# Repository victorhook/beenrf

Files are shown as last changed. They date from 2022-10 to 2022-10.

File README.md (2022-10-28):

# BeeNrf BeeNrf logo

## How to get started with EFM8B Busy Bee Ubuntu 22.04

### 1. Install stable wine.
Install wine according to winehq: https://wiki.winehq.org/Ubuntu
Don't follow normal ubuntu guidelines, since it requires manually installing `wine32`
which wants to break half of my system.

### 2. Launch
cd $SIMPLICITY_INSTALLATION && WINEPATH=$SIMPLICITY_INSTALLATION ./studio

## BOM
| Geared 3V motor x2 | 32kr * 2 |
| Front wheel |  |
| nrf24l01 | 18kr | 
| Busy Bee 8-bit | 10kr |
| Mosfet | 2 |
| Battery charg | |

## PCB Layers
1. RF signals
2. Ground  <- Don't break!
3. Power   <- Don't break!
4. Other signals

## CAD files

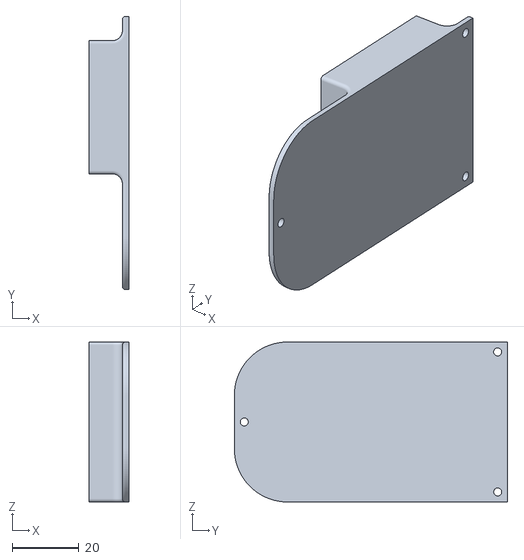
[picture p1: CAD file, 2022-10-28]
cad/Robot-Top.stl
12.0 x 82.0 x 48.0

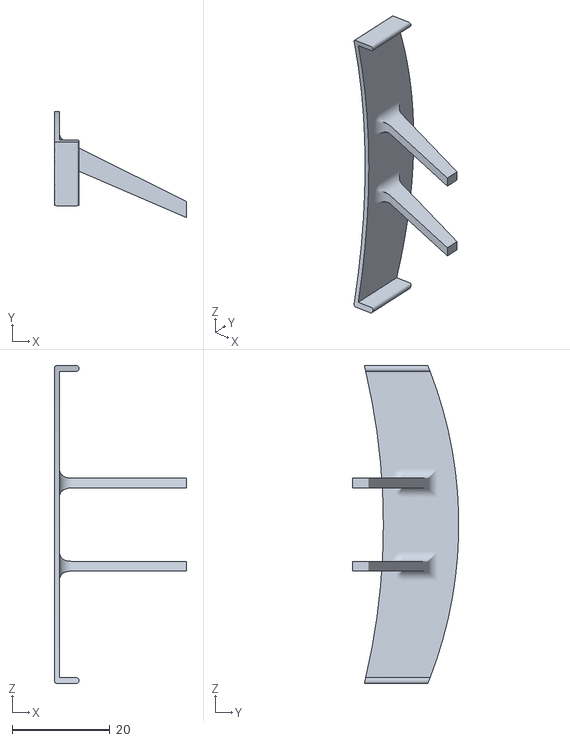
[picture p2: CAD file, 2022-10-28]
cad/Robot-Spoiler.stl
27.0 x 21.7 x 65.0

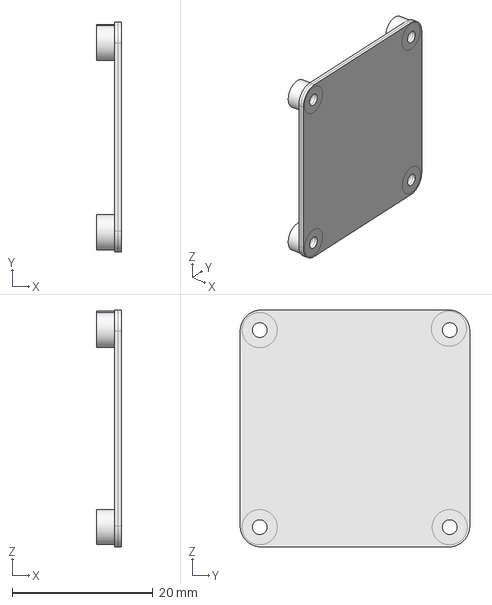
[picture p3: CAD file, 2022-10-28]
cad/Robot.FCStd
3.50 x 32.6 x 33.7 mm

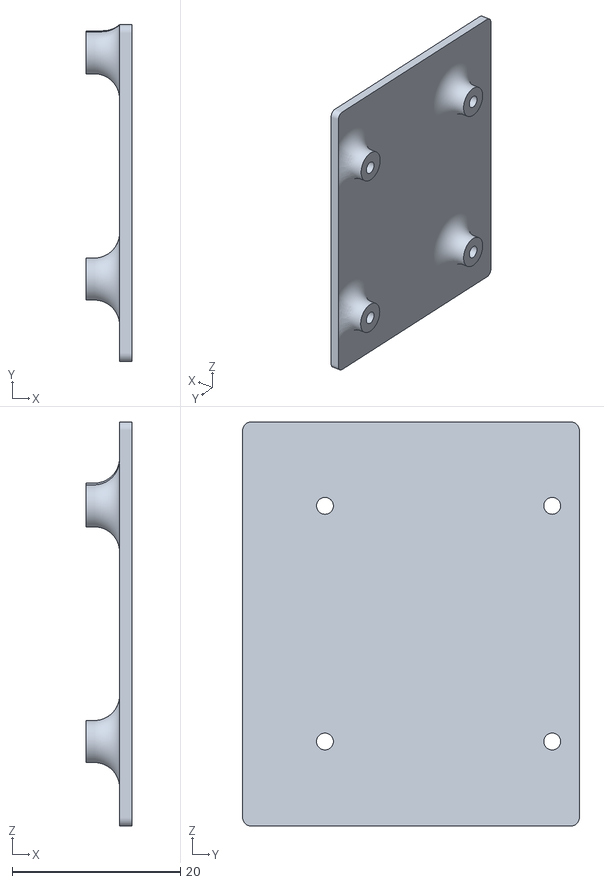
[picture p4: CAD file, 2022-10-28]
cad/Robot-TopsTop.stl
5.50 x 40.0 x 48.0

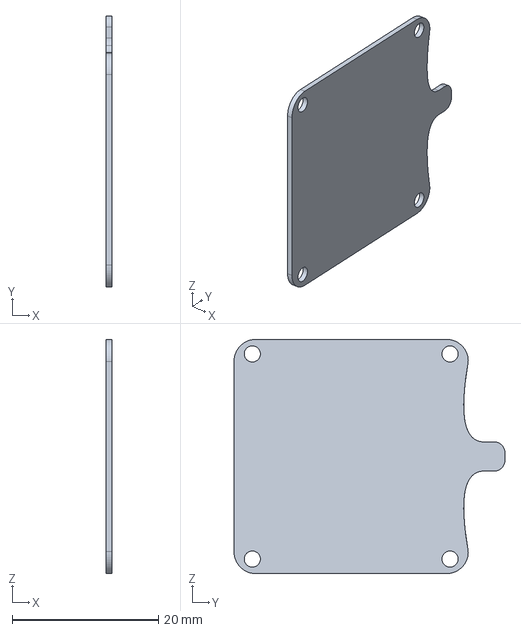
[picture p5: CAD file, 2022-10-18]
cad/Fillet004.step
0.8 x 37.0 x 32.0 mm

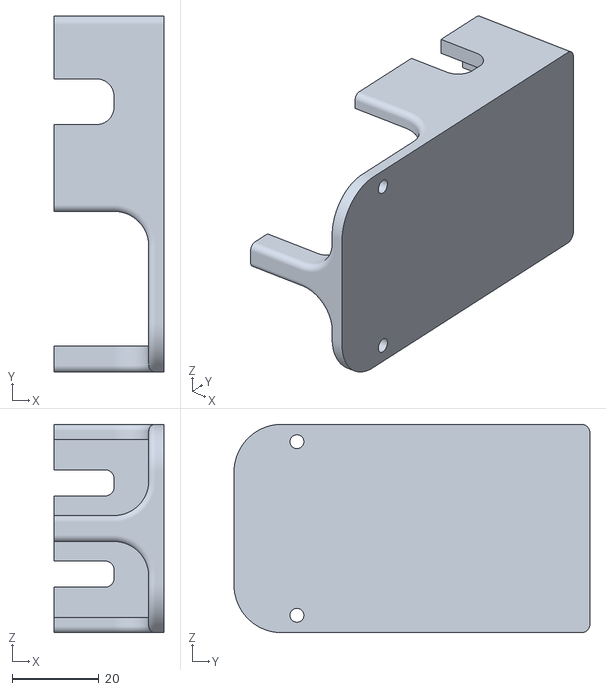
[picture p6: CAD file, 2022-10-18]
cad/Robot-Bottom.stl
25.3 x 82.0 x 48.0

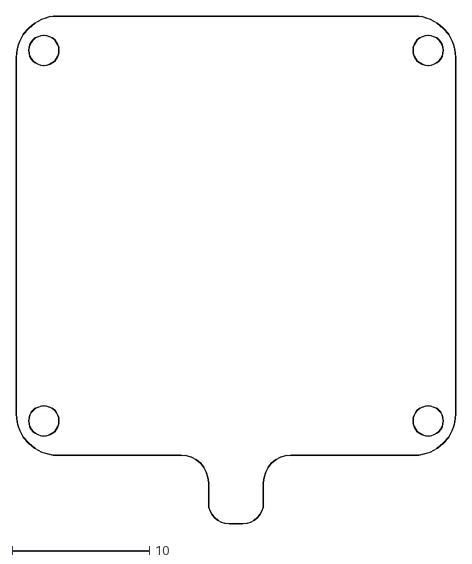
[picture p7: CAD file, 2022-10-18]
cad/PCB.dxf
32.0 x 37.0

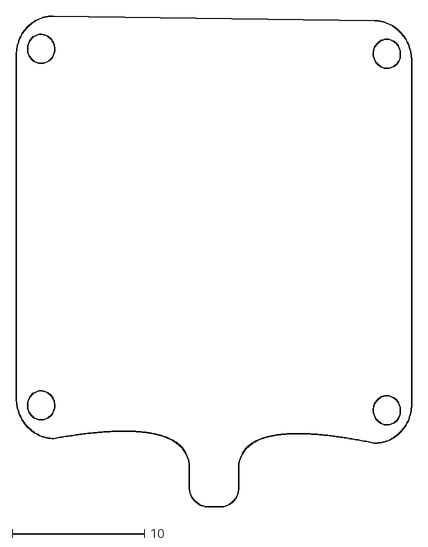
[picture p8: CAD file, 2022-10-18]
cad/Robot-Shape2DView002.dxf
29.9 x 37.2

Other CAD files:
cad/Robot-TopTopTop.stl

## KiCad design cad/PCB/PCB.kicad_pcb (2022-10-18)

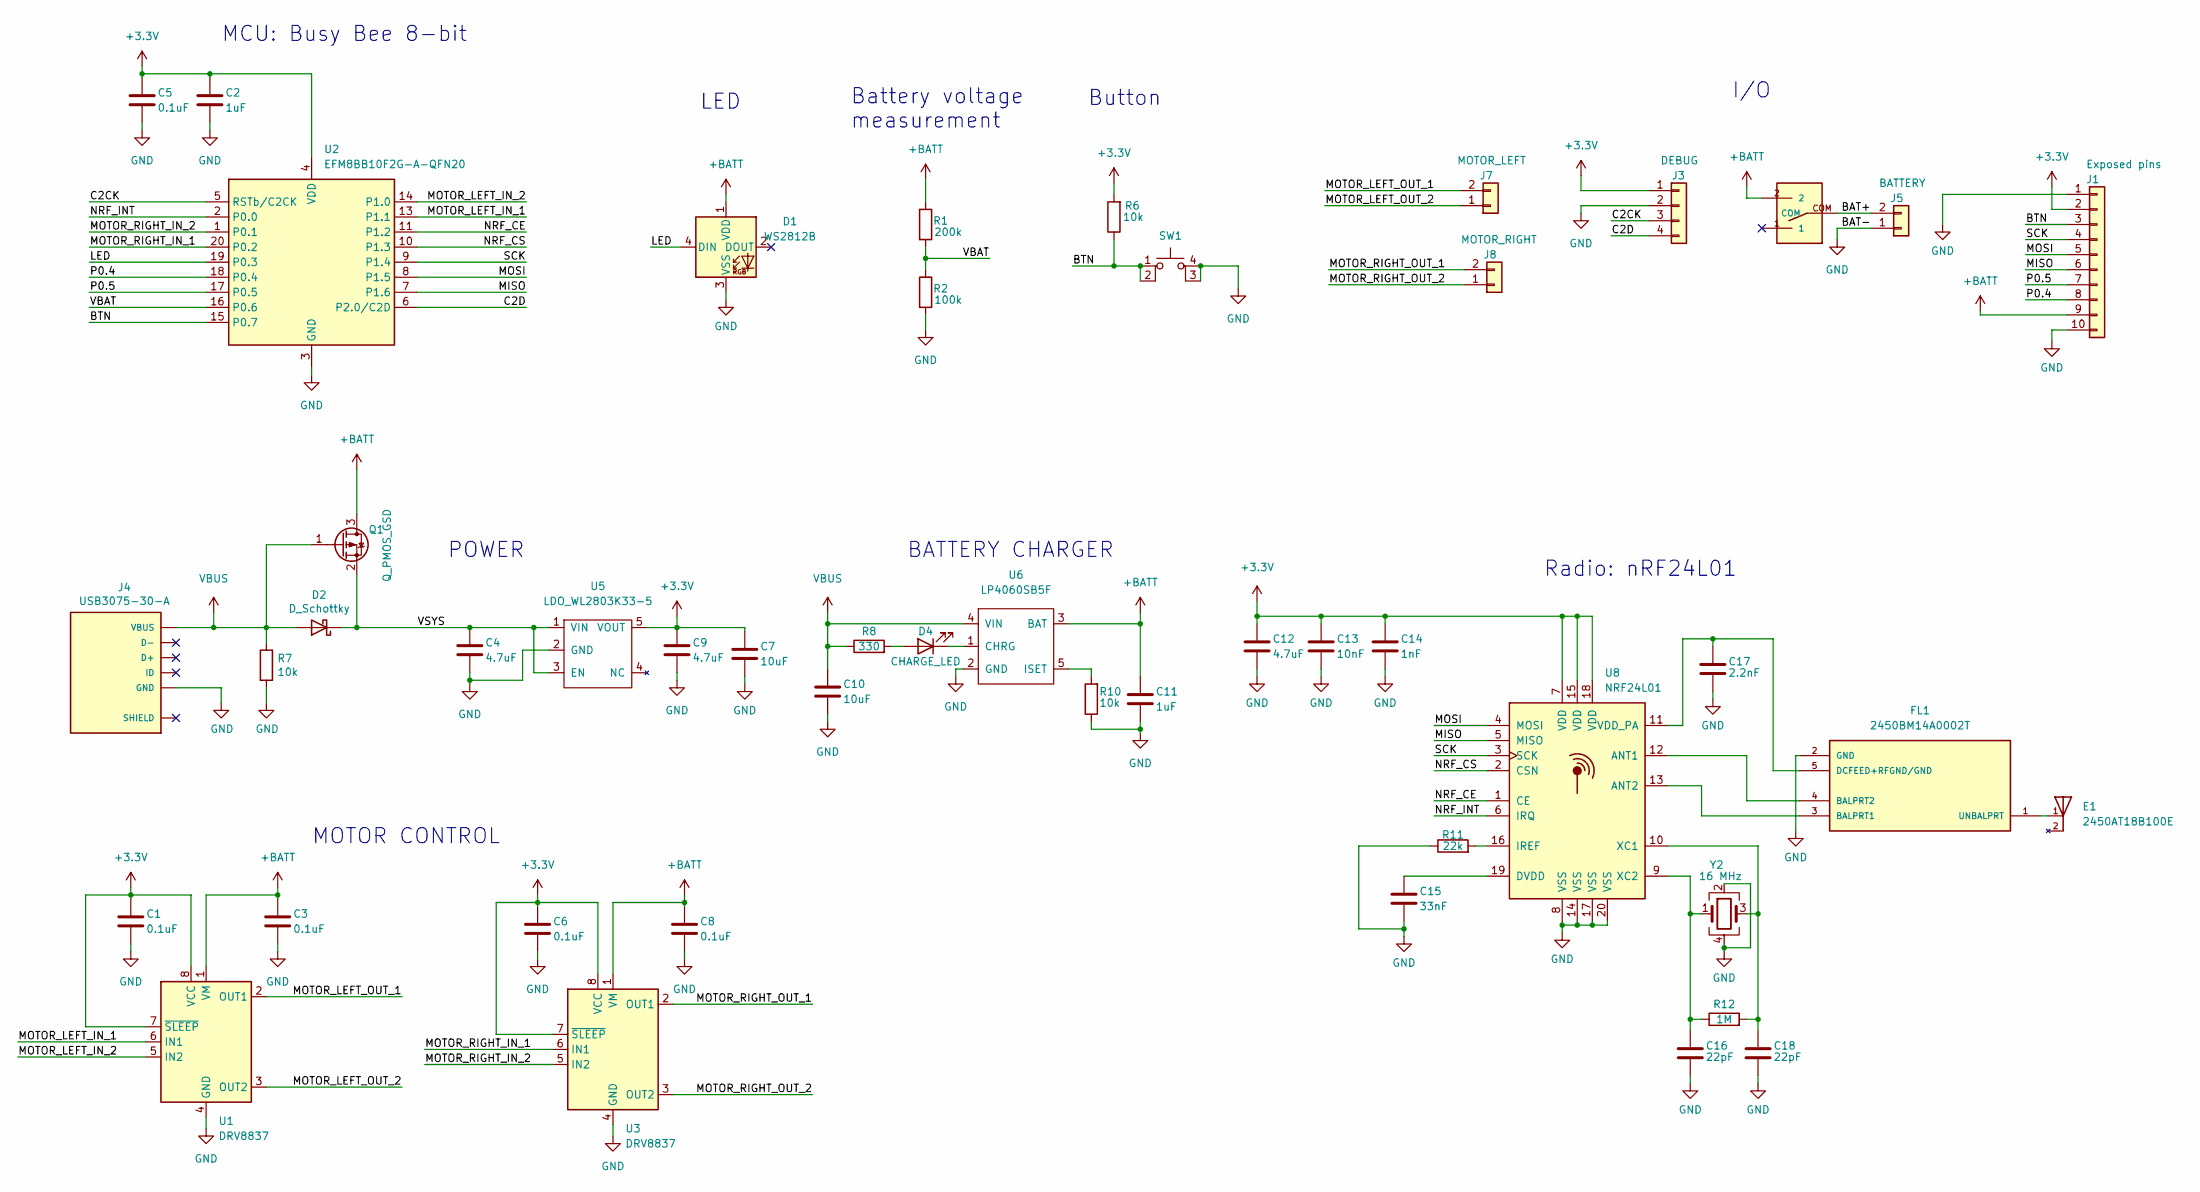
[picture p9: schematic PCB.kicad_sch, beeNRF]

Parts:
C1, C3, C5, C6, C8: 0.1uF; C_0402_1005Metric
C2, C11: 1uF; C_0402_1005Metric
C4, C9, C12: 4.7uF; C_0402_1005Metric
C7, C10: 10uF; C_0805_2012Metric
C13: 10nF; C_0402_1005Metric
C14: 1nF; C_0402_1005Metric
C15: 33nF; C_0402_1005Metric
C16, C18: 22pF; C_0402_1005Metric
C17: 2.2nF; C_0402_1005Metric
D1: WS2812B; LED_WS2812B_PLCC4_5.0x5.0mm_P3.2mm
D2: D_Schottky; D_SOD-123
D4: CHARGE_LED; LED_0603_1608Metric
E1: 2450AT18B100E; 2450AT18B100E_pcb_antenna; PARTREV 4.0
FL1: 2450BM14A0002T; 2450BM14A0002; PARTREV 6/13/2012
J1: Exposed pins; PinSocket_1x10_P2.54mm_Vertical
J3: DEBUG; JST_SH_SM04B-SRSS-TB_1x04-1MP_P1.00mm_Horizontal_No_silk
J4: USB3075-30-A; PARTREV D3
J5: BATTERY; Conn_01x02_VBAT
J7: MOTOR_LEFT; Conn_01x02_VBAT
J8: MOTOR_RIGHT; Conn_01x02_VBAT
Q1: Q_PMOS_GSD; SOT-23
R1: 200k; R_0402_1005Metric
R2: 100k; R_0402_1005Metric
R6, R7, R10: 10k; R_0402_1005Metric
R8: 330; R_0402_1005Metric
R11: 22k; R_0402_1005Metric
R12: 1M; R_0402_1005Metric
SW1: RESET; PTS815
U1, U3: DRV8837; WSON-8-1EP_2x2mm_P0.5mm_EP0.9x1.6mm
U2: EFM8BB10F2G-A-QFN20; SiliconLabs_QFN-20-1EP_3x3mm_P0.5mm_EP1.8x1.8mm
U5: LDO_WL2803K33-5; SOT-89-5
U6: LP4060SB5F; SOT-23-5
U7: SK12D07VG4; toggle_switch_SK12D07VG4
U8: NRF24L01; QFN-20-1EP_4x4mm_P0.5mm_EP2.5x2.5mm
Y2: 16 MHz; Crystal_SMD_2520-4Pin_2.5x2.0mm

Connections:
+3.3V: C1.1, C2.1, C5.1, C6.1, C7.1, C9.1, C12.1, C13.1, C14.1, J1.2, J3.1, R6.2, U1.7 (~SLEEP), U1.8 (VCC), U2.4 (VDD), U3.7 (~SLEEP), U3.8 (VCC), U5.5 (VOUT), U8.7 (VDD), U8.15 (VDD), U8.18 (VDD)
+BATT: C3.1, C8.1, C11.1, D1.1 (VDD), J1.9, Q1.3 (D), R1.1, U1.1 (VM), U3.1 (VM), U6.3 (BAT), U7.2
/BAT+: J5.2, U7.COM
/BTN: J1.3, R6.1, SW1.1, SW1.2, U2.15 (P0.7)
/C2CK: J3.3, U2.5 (RSTb/C2CK)
/C2D: J3.4, U2.6 (P2.0/C2D)
/LED: D1.4 (DIN), U2.19 (P0.3)
/MISO: J1.6, U2.7 (P1.6), U8.5 (MISO)
/MOSI: J1.5, U2.8 (P1.5), U8.4 (MOSI)
/MOTOR_LEFT_IN_1: U1.6 (IN1), U2.13 (P1.1)
/MOTOR_LEFT_IN_2: U1.5 (IN2), U2.14 (P1.0)
/MOTOR_LEFT_OUT_1: J7.2, U1.2 (OUT1)
/MOTOR_LEFT_OUT_2: J7.1, U1.3 (OUT2)
/MOTOR_RIGHT_IN_1: U2.20 (P0.2), U3.6 (IN1)
/MOTOR_RIGHT_IN_2: U2.1 (P0.1), U3.5 (IN2)
/MOTOR_RIGHT_OUT_1: J8.2, U3.2 (OUT1)
/MOTOR_RIGHT_OUT_2: J8.1, U3.3 (OUT2)
/NRF_CE: U2.11 (P1.2), U8.1 (CE)
/NRF_CS: U2.10 (P1.3), U8.2 (CSN)
/NRF_INT: U2.2 (P0.0), U8.6 (IRQ)
/P0.4: J1.8, U2.18 (P0.4)
/P0.5: J1.7, U2.17 (P0.5)
/SCK: J1.4, U2.9 (P1.4), U8.3 (SCK)
/VBAT: R1.2, R2.1, U2.16 (P0.6)
/VSYS: C4.1, D2.1 (K), Q1.2 (S), U5.1 (VIN), U5.3 (EN)
GND: C1.2, C2.2, C3.2, C4.2, C5.2, C6.2, C7.2, C8.2, C9.2, C10.2, C11.2, C12.2, C13.2, C14.2, C15.2, C16.2, C17.2, C18.2, D1.3 (VSS), FL1.2 (GND), J1.1, J1.10, J3.2, J4.5 (GND), J5.1, R2.2, R7.2, R10.1, R11.1, SW1.3 (K), SW1.4 (A), U1.4 (GND), U1.9 (GND), U2.3 (GND), U2.12 (GND), U2.21 (GND), U3.4 (GND), U3.9 (GND), U5.2 (GND), U6.2 (GND), U8.8 (VSS), U8.14 (VSS), U8.17 (VSS), U8.20 (VSS), Y2.2, Y2.4
unnamed: C15.1, U8.19 (DVDD)
unnamed: C16.1, R12.1, U8.9 (XC2), Y2.1
unnamed: C17.1, FL1.5 (DCFEED+RFGND/GND), U8.11 (VDD_PA)
unnamed: C18.1, R12.2, U8.10 (XC1), Y2.3
unnamed: D4.1 (K), U6.1 (CHRG)
unnamed: D4.2 (A), R8.2
unnamed: E1.1, FL1.1 (UNBALPRT)
unnamed: FL1.3 (BALPRT1), U8.13 (ANT2)
unnamed: FL1.4 (BALPRT2), U8.12 (ANT1)
unnamed: R10.2, U6.5 (ISET)
unnamed: R11.2, U8.16 (IREF)
VBUS: C10.1, D2.2 (A), J4.1 (VBUS), Q1.1 (G), R7.1, R8.1, U6.4 (VIN)

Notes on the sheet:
Battery voltage measurement
BATTERY CHARGER
I/O
MCU: Busy Bee 8-bit
Radio: nRF24L01
MOTOR CONTROL
LED
POWER
Button

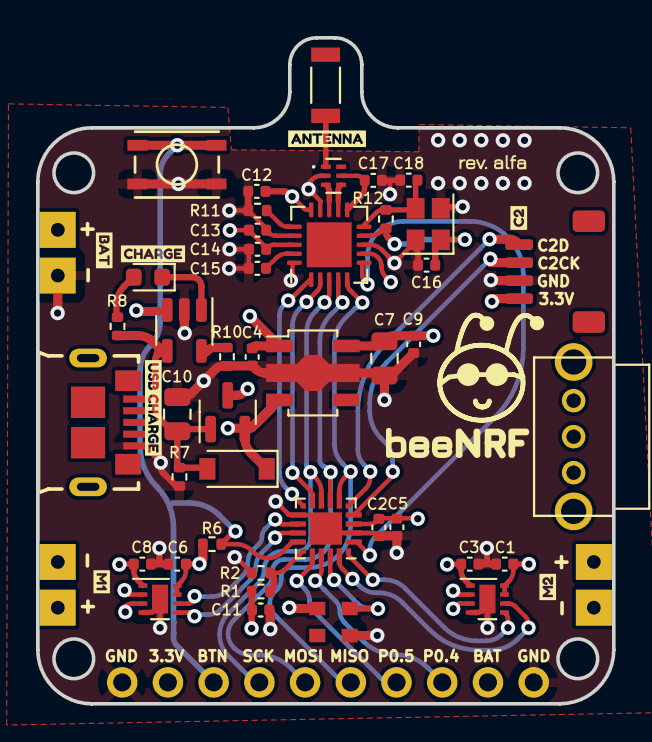
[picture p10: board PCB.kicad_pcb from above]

Board: 4 copper layers, 32.0 x 37.0 mm, 54 parts (0 on the bottom side), 38 nets.

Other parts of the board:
kibuzzard-63246B6F: G***; kibuzzard-63246B6F
kibuzzard-63246BBB: G***; kibuzzard-63246BBB
kibuzzard-63246BF5: G***; kibuzzard-63246BF5
kibuzzard-63246C29: G***; kibuzzard-63246C29
kibuzzard-63247AD7: G***; kibuzzard-63247AD7
kibuzzard-63247AF7: G***; kibuzzard-63247AF7
kibuzzard-63247D50: G***; kibuzzard-63247D50

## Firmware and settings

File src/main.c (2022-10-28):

#include "core.h"
#include "radio.h"
#include "led.h"
#include "motor_control.h"


// --- Note: For sdcc, we MUST define all ISRs in main file! --- #

/* Main systick timer */
SI_INTERRUPT(TIMER1_ISR, TIMER1_IRQn);

/* Button reset */
SI_INTERRUPT(INT0_ISR, INT0_IRQn);

/* PWM Interrupt */
SI_INTERRUPT(PCA0_ISR, PCA0_IRQn);


int main() {
  sys_init();
  led_init();
  radio_init();
  motor_control_init();

  while (1) {
    radio_update();
    motor_control_update();
    led_set(0);
  }

  return 0;
}

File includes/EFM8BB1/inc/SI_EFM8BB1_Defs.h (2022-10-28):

//------------------------------------------------------------------------------
// Copyright 2014 Silicon Laboratories, Inc.
// All rights reserved. This program and the accompanying materials
// are made available under the terms of the Silicon Laboratories End User
// License Agreement which accompanies this distribution, and is available at
// http://developer.silabs.com/legal/version/v11/Silicon_Labs_Software_License_Agreement.txt
// Original content and implementation provided by Silicon Laboratories.
//------------------------------------------------------------------------------
//Supported Devices:
//  EFM8BB10F2A_QFN20
//  EFM8BB10F2G_QFN20
//  EFM8BB10F2I_QFN20
//  EFM8BB10F4A_QFN20
//  EFM8BB10F4G_QFN20
//  EFM8BB10F4I_QFN20
//  EFM8BB10F8A_QFN20
//  EFM8BB10F8G_QFN20
//  EFM8BB10F8G_QSOP24
//  EFM8BB10F8G_SOIC16
//  EFM8BB10F8I_QFN20
//  EFM8BB10F8I_QSOP24
//  EFM8BB10F8I_SOIC16

#ifndef SI_EFM8BB1_DEFS_H
#define SI_EFM8BB1_DEFS_H

#include <si_toolchain.h>

//-----------------------------------------------------------------------------
// Register Definitions
//-----------------------------------------------------------------------------
SI_SFR (ACC,      0xE0); ///< Accumulator                            
SI_SFR (ADC0AC,   0xB3); ///< ADC0 Accumulator Configuration         
SI_SFR (ADC0CF,   0xBC); ///< ADC0 Configuration                     
SI_SFR (ADC0CN0,  0xE8); ///< ADC0 Control 0                         
SI_SFR (ADC0CN1,  0xB2); ///< ADC0 Control 1                         
SI_SFR (ADC0GTH,  0xC4); ///< ADC0 Greater-Than High Byte            
SI_SFR (ADC0GTL,  0xC3); ///< ADC0 Greater-Than Low Byte             
SI_SFR (ADC0H,    0xBE); ///< ADC0 Data Word High Byte               
SI_SFR (ADC0L,    0xBD); ///< ADC0 Data Word Low Byte                
SI_SFR (ADC0LTH,  0xC6); ///< ADC0 Less-Than High Byte               
SI_SFR (ADC0LTL,  0xC5); ///< ADC0 Less-Than Low Byte                
SI_SFR (ADC0MX,   0xBB); ///< ADC0 Multiplexer Selection             
SI_SFR (ADC0PWR,  0xDF); ///< ADC0 Power Control                     
SI_SFR (ADC0TK,   0xB9); ///< ADC0 Burst Mode Track Time             
SI_SFR (B,        0xF0); ///< B Register                             
SI_SFR (CKCON0,   0x8E); ///< Clock Control 0                        
SI_SFR (CLKSEL,   0xA9); ///< Clock Select                           
SI_SFR (CMP0CN0,  0x9B); ///< Comparator 0 Control 0                 
SI_SFR (CMP0MD,   0x9D); ///< Comparator 0 Mode                      
SI_SFR (CMP0MX,   0x9F); ///< Comparator 0 Multiplexer Selection     
SI_SFR (CMP1CN0,  0xBF); ///< Comparator 1 Control 0                 
SI_SFR (CMP1MD,   0xAB); ///< Comparator 1 Mode                      
SI_SFR (CMP1MX,   0xAA); ///< Comparator 1 Multiplexer Selection     
SI_SFR (CRC0AUTO, 0xD2); ///< CRC0 Automatic Control                 
SI_SFR (CRC0CN0,  0xCE); ///< CRC0 Control 0                         
SI_SFR (CRC0CNT,  0xD3); ///< CRC0 Automatic Flash Sector Count      
SI_SFR (CRC0DAT,  0xDE); ///< CRC0 Data Output                       
SI_SFR (CRC0FLIP, 0xCF); ///< CRC0 Bit Flip                          
SI_SFR (CRC0IN,   0xDD); ///< CRC0 Data Input                        
SI_SFR (DERIVID,  0xAD); ///< Derivative Identification              
SI_SFR (DEVICEID, 0xB5); ///< Device Identification                  
SI_SFR (DPH,      0x83); ///< Data Pointer High                      
SI_SFR (DPL,      0x82); ///< Data Pointer Low                       
SI_SFR (EIE1,     0xE6); ///< Extended Interrupt Enable 1            
SI_SFR (EIP1,     0xF3); ///< Extended Interrupt Priority 1          
SI_SFR (FLKEY,    0xB7); ///< Flash Lock and Key                     
SI_SFR (HFO0CAL,  0xC7); ///< High Frequency Oscillator 0 Calibration
SI_SFR (IE,       0xA8); ///< Interrupt Enable                       
SI_SFR (IP,       0xB8); ///< Interrupt Priority                     
SI_SFR (IT01CF,   0xE4); ///< INT0/INT1 Configuration                
SI_SFR (LFO0CN,   0xB1); ///< Low Frequency Oscillator Control       
SI_SFR (P0,       0x80); ///< Port 0 Pin Latch                       
SI_SFR (P0MASK,   0xFE); ///< Port 0 Mask                            
SI_SFR (P0MAT,    0xFD); ///< Port 0 Match                           
SI_SFR (P0MDIN,   0xF1); ///< Port 0 Input Mode                      
SI_SFR (P0MDOUT,  0xA4); ///< Port 0 Output Mode                     
SI_SFR (P0SKIP,   0xD4); ///< Port 0 Skip                            
SI_SFR (P1,       0x90); ///< Port 1 Pin Latch                       
SI_SFR (P1MASK,   0xEE); ///< Port 1 Mask                            
SI_SFR (P1MAT,    0xED); ///< Port 1 Match                           
SI_SFR (P1MDIN,   0xF2); ///< Port 1 Input Mode                      
SI_SFR (P1MDOUT,  0xA5); ///< Port 1 Output Mode                     
SI_SFR (P1SKIP,   0xD5); ///< Port 1 Skip                            
SI_SFR (P2,       0xA0); ///< Port 2 Pin Latch
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

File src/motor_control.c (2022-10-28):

#include "motor_control.h"
#include "core.h"
#include "state.h"


//#define PCA_DIFF 4083  // PWM Frequency 500 HZ, Period: 2ms
#define PCA_DIFF 4083
#define PCA_MAX  0xffff
#define PCA_MIN  (PCA_MAX - PCA_DIFF)

// Helper defines
#define set_pwm_m1(value) set_sfr_16(PCA0CPL0, PCA0CPH0, PCA_MIN+value)
#define set_pwm_m2(value) set_sfr_16(PCA0CPL1, PCA0CPH1, PCA_MIN+value)

#define MOTOR_NOT_BEING_PWM_VALUE 1

#define XBAR_MOTOR_LEFT  P1SKIP
#define XBAR_MOTOR_RIGHT P0SKIP

#define XBAR_MOTOR_LEFT_1 (P1SKIP_B0__SKIPPED | P1SKIP_B1__NOT_SKIPPED | P1SKIP_B2__SKIPPED | P1SKIP_B3__SKIPPED | P1SKIP_B4__SKIPPED | P1SKIP_B5__SKIPPED | P1SKIP_B6__SKIPPED | P1SKIP_B7__SKIPPED)
#define XBAR_MOTOR_LEFT_2 (P1SKIP_B0__NOT_SKIPPED | P1SKIP_B1__SKIPPED | P1SKIP_B2__SKIPPED | P1SKIP_B3__SKIPPED | P1SKIP_B4__SKIPPED | P1SKIP_B5__SKIPPED | P1SKIP_B6__SKIPPED | P1SKIP_B7__SKIPPED)

#define XBAR_MOTOR_RIGHT_1 (P0SKIP_B0__SKIPPED | P0SKIP_B1__SKIPPED | P0SKIP_B2__NOT_SKIPPED | P0SKIP_B3__SKIPPED | P0SKIP_B4__SKIPPED | P0SKIP_B5__SKIPPED | P0SKIP_B6__SKIPPED | P0SKIP_B7__SKIPPED)
#define XBAR_MOTOR_RIGHT_2 (P0SKIP_B0__SKIPPED | P0SKIP_B1__NOT_SKIPPED | P0SKIP_B2__SKIPPED | P0SKIP_B3__SKIPPED | P0SKIP_B4__SKIPPED | P0SKIP_B5__SKIPPED | P0SKIP_B6__SKIPPED | P0SKIP_B7__SKIPPED)

typedef enum {
  STEER_DIRECTION_RIGHT,
  STEER_DIRECTION_LEFT,
  STEER_DIRECTION_STRAIGHT
} steer_direction_t;

typedef enum {
  MOTOR_DIRECTION_FORWARD,
  MOTOR_DIRECTION_BACKWARD,
  MOTOR_DIRECTION_IDLE
} motor_direction_t;


// --- Helper functions --- //

#define pwm_disable() (PCA0CN0 = PCA0CN0_CR__STOP)

#define pwm_enable()  (PCA0CN0 = PCA0CN0_CR__RUN)

#define motors_off() \
  pwm_disable(); \
  P0SKIP = 0xff; \
  P1SKIP = 0xff; \
  PIN_MOTOR_RIGHT_2 = 0; \
  PIN_MOTOR_RIGHT_1 = 0; \
  PIN_MOTOR_LEFT_2  = 0; \
  PIN_MOTOR_LEFT_1  = 0;

static void route_pwm(const motor_direction_t motor_right, const motor_direction_t motor_left);

static void set_steer_direction(const steer_direction_t steer_direction, const motor_direction_t motor_direction) ;


status_t motor_control_init() {
    // PCA Initialization (for PWM)
    PCA0MD = PCA0MD_CPS__SYSCLK_DIV_12 |    // Set clock source
             PCA0MD_ECF__OVF_INT_ENABLED;   // Enabled interrupt on Timer/Counter Overflow
    // PCA 0
    PCA0CPM0 = PCA0CPM0_PWM16__16_BIT |     // 16-bit PWM
               PCA0CPM0_PWM__ENABLED;//  |     // Enable PWM

    // PCA 1
    PCA0CPM1 = PCA0CPM1_PWM16__16_BIT |     // 16-bit PWM
               PCA0CPM1_PWM__ENABLED;// |      // Enable PWM

    PCA0POL = PCA0POL_CEX0POL__INVERT | PCA0POL_CEX1POL__INVERT;

    PCA0CN0 = PCA0CN0_CR__RUN;              // Start PCA

    XBR1 |= XBR1_PCA0ME__CEX0_CEX1;

    // Enable interrupt
    EIE1 |= EIE1_EPCA0__ENABLED;

    // Initial value
    set_steer_direction(STEER_DIRECTION_STRAIGHT, MOTOR_DIRECTION_FORWARD);
    set_pwm_m1(0);
    set_pwm_m2(0);

    return STATUS_OK;
}


// BACK  IDLE   FORWARD
// 0     2041   4082
#define MOTOR_IDLE 2041

void motor_control_update() {
  //   XIN1    XIN2   Function
  //   PWM     0      Forward PWM, fast decay
  //   1       PWM    Forward PWM, slow decay
  //   0       PWM    Reverse PWM, fast decay
  //   PWM     1      Reverse PWM, slow decay


  // Update state
  state.current.steer = state.target.steer;
  state.current.thrust = state.target.thrust;

  steer_direction_t steer_direction;
  motor_direction_t motor_direction;
  uint16_t thrust;

  // Steering
  if (state.current.steer == MOTOR_IDLE)
  {
    steer_direction = STEER_DIRECTION_STRAIGHT;
  }
  else if (state.current.steer > MOTOR_IDLE)
  {
    steer_direction = STEER_DIRECTION_RIGHT;
  }
  else
  {
    steer_direction = STEER_DIRECTION_LEFT;
  }

  // Motor thrust
  if (state.current.thrust == MOTOR_IDLE)
  {
    motor_direction = MOTOR_DIRECTION_IDLE;
  }
  else if (state.current.thrust > MOTOR_IDLE)
  {
    motor_direction = MOTOR_DIRECTION_FORWARD;
    thrust = state.current.thrust - MOTOR_IDLE;
  }
  else
  {
    motor_direction = MOTOR_DIRECTION_BACKWARD;
    thrust = MOTOR_IDLE - state.current.thrust;
  }

  /*
  if (motor_direction == MOTOR_DIRECTION_IDLE)
  {
    PIN_MOTOR_LEFT_1 = 0;
    PIN_MOTOR_LEFT_2 = 0;
    PIN_MOTOR_RIGHT_1 = 0;
    PIN_MOTOR_RIGHT_2 = 0;
  }
  else if (motor_direction == MOTOR_DIRECTION_FORWARD)
  {
    PIN_MOTOR_LEFT_1 = 0;
    PIN_MOTOR_LEFT_2 = 1;
    PIN_MOTOR_RIGHT_1 = 0;
    PIN_MOTOR_RIGHT_2 = 1;
  }
  else if (motor_direction == MOTOR_DIRECTION_BACKWARD)
  {
    PIN_MOTOR_LEFT_1 = 1;
    PIN_MOTOR_LEFT_2 = 0;
    PIN_MOTOR_RIGHT_1 = 1;
    PIN_MOTOR_RIGHT_2 = 0;
  }
  */


  if (motor_direction == MOTOR_DIRECTION_IDLE && steer_direction == STEER_DIRECTION_STRAIGHT)
  {
    motors_off();
  }
  else
  {
    pwm_disable();
    set_steer_direction(steer_direction, motor_direction);

    if (motor_direction == MOTOR_DIRECTION_IDLE)
    {
      // We'll just spin on the spot, wheels going opposite direction.
      if (state.current.steer > MOTOR_IDLE)
      {
        thrust = state.current.steer - MOTOR_IDLE;
      }
      else
      {
        thrust = MOTOR_IDLE - state.current.steer;
      }
    }

    // Multiply with 2 to put thrust into correct PWM range (0-4082).
    thrust = (MOTOR_IDLE - thrust) << 1;

    set_pwm_m1(thrust);
    set_pwm_m2(thrust);

    pwm_enable();


  }

  delay(10);
}



static void route_pwm(const motor_direction_t motor_right, const motor_direction_t motor_left)
{
  // Right
  if (motor_right == MOTOR_DIRECTION_FORWARD)
  {
    XBAR_MOTOR_RIGHT = XBAR_MOTOR_RIGHT_1;
    PIN_MOTOR_RIGHT_2 = MOTOR_NOT_BEING_PWM_VALUE;
  }
  else if (motor_right == MOTOR_DIRECTION_BACKWARD)
  {
    XBAR_MOTOR_RIGHT = XBAR_MOTOR_RIGHT_2;
    PIN_MOTOR_RIGHT_1 = MOTOR_NOT_BEING_PWM_VALUE;
  }

  // Left
  if (motor_left == MOTOR_DIRECTION_FORWARD)
  {
    XBAR_MOTOR_LEFT = XBAR_MOTOR_LEFT_1;
    PIN_MOTOR_LEFT_2 = MOTOR_NOT_BEING_PWM_VALUE;
  }
  else if (motor_left == MOTOR_DIRECTION_BACKWARD)
  {
    XBAR_MOTOR_LEFT = XBAR_MOTOR_LEFT_2;
    PIN_MOTOR_LEFT_1 = MOTOR_NOT_BEING_PWM_VALUE;
  }

  //PIN_MOTOR_LEFT_1 = MOTOR_NOT_BEING_PWM_VALUE;
  //PIN_MOTOR_LEFT_2 = MOTOR_NOT_BEING_PWM_VALUE;
  //PIN_MOTOR_RIGHT_1 = MOTOR_NOT_BEING_PWM_VALUE;
  //PIN_MOTOR_RIGHT_2 = MOTOR_NOT_BEING_PWM_VALUE;
}

static void set_steer_direction(const steer_direction_t steer_direction, const motor_direction_t motor_direction) {
  switch (motor_direction)
  {
    case MOTOR_DIRECTION_FORWARD:
      route_pwm(MOTOR_DIRECTION_FORWARD, MOTOR_DIRECTION_FORWARD);
      break;
    case MOTOR_DIRECTION_BACKWARD:
      route_pwm(MOTOR_DIRECTION_BACKWARD, MOTOR_DIRECTION_BACKWARD);
      break;
    case MOTOR_DIRECTION_IDLE:
      if (steer_direction == STEER_DIRECTION_RIGHT)
      {
        route_pwm(MOTOR_DIRECTION_BACKWARD, MOTOR_DIRECTION_FORWARD);
      }
      else if (steer_direction == STEER_DIRECTION_LEFT)
      {
        route_pwm(MOTOR_DIRECTION_FORWARD, MOTOR_DIRECTION_BACKWARD);
      }
      break;
  }

}
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

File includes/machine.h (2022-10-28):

#ifndef MACHINE_H
#define MACHINE_H

#include "core.h"


#define PIN_NRF_INT       P0_B0
#define PIN_MOTOR_RIGHT_2 P0_B1  // M2
#define PIN_MOTOR_RIGHT_1 P0_B2  // M2
#define PIN_VBAT          P0_B6
#define PIN_BTN           P0_B7
#define PIN_MOTOR_LEFT_2  P1_B0
#define PIN_MOTOR_LEFT_1  P1_B1


//#define DEV_BOARD

#ifdef DEV_BOARD
    // Local devboard
    #define PIN_LED           P1_B4

    // SPI
    #define PIN_NRF_CE P1_B5
    #define PIN_NRF_CS P1_B6
    #define PIN_SCK    P1_B7
    #define PIN_MOSI   P1_B3
    #define PIN_MISO   P1_B2
#else
    // Real BeeNRF
    #define PIN_LED           P0_B3

    // SPI
    #define PIN_NRF_CE        P1_B2
    #define PIN_NRF_CS        P1_B3
    #define PIN_SCK           P1_B4
    #define PIN_MOSI          P1_B5
    #define PIN_MISO          P1_B6
#endif


#endif /* MACHINE_H */

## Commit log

2022-10-18 Just saving cad files
    [Fillet004.step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]
2022-10-28 Moved project to different directory. Most basic functionality of the robot is working. There's some fine-tuning to do!
    [Robot-Spoiler.stl, Robot-Top.stl, Robot-TopTopTop.stl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]

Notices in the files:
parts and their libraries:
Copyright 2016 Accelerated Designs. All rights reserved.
